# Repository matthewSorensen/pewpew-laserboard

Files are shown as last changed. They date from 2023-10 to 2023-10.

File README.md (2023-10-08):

# PewPew LaserBoard

## What Is It?

LaserBoard is an open source controller for fiber laser marking systems, based around a Teensy 4.1 MCU board. LaserBoard
provides a USB interface compatible with most low-cost fiber laser sources and XY-100-speaking galvanometer scanners, and
supports 4 axes of step/direction motion control. LaserBoard is released under the terms of CERN-OHL-S; see LICENSE.txt,
or [cern_ohl_s_v2.txt](https://ohwr.org/cern_ohl_s_v2.txt) for the full text.

## Q&A

### Why?

At the component level, laser marking hardware is remarkably cheap and high quality, and easy to interface with. Sadly, laser
marker control boards aren't! Generally, they're bundled with a license for low-quality, proprietary software,
greatly inflating the price - a control board with 4 auxiliary axes (eg. JCZ DLC2-M4) cost about as much as a quality
laser source and scanner ($2000!).

Advanced features such as high-precision lens calibration, field stitching, active z-axes control etc. are also very
difficult to implement, as the commercial controllers behave like a black-box and speak an undocumented host/controller
protocol. Some reverse-engineered 3rd party software exists, such as [LightBurn](https://lightburnsoftware.com/) (commercial,
user-friendly high-quality GUI) or [Balor](https://www.bryce.pw/engraver.html) (open-source python interface library),
but controller support is limited.

### Lasers Are Dangerous! Is This Safe?

Lasers can be very dangerous! Unenclosed 10+ watt invisible lasers with peak powers in the low 10s of kW are
absolutely not safe, and a quick scan of YouTokstagram "laser influencer" content will show many poorly educated people
doing very dangerous things with them. Laser safety regulation and enforcement hasn't caught up to the ease with
which anyone can import a turnkey class-4 laser capable of instablindess.

Lasers are also very useful and all of the risks associated with them may be mitigated with proper engineering and
procedural controls. It is essential to fully understand these risks BEFORE purchasing a laser, and if you already
have one, before modifying it or further using it.

If you're in a context with a laser safety officer, talk with them. Laser safety officers are your friends, even
if they seem scary at first.

### What Software Do I Need?

LaserBoard is designed for use with [pewpew-laser](https://github.com/matthewSorensen/pewpew-laser). If that link
appears to be a 404, it's because I'm ambivalent about running an open-source project and haven't figured out the
liability issues related to releasing a complete system. Additionally, there's no GUI or even a standard toolpath
generation script - although there might be some [Rhinoceros](https://www.rhino3d.com/) plugins in the works.

### What Hardware Do I Need?

The following table provides an estimate for a minimal laser marking system with a small Q-switched laser
source, a 50x50 working envelope, a mid-market galvo scanner, and a manually-focused z axis.

|Component |Example Manufacturer and PN|Budgetary Price |
|---|---|---|
|Control Board PCB | LaserBoard-Rev5 |$5-50 |
|Control Board Components | Mouser | $90 |
|30W Laser Source | Raycus - RFL-P30QS | $1000 |
|Galvo Scanner | Sino-Galvo SG7110 | $400 |
|F-theta Lens | HY-SL-1064-50-63 | $70 |
|Beam Path | "Fiber Laser Beam Path" | $70 |
|Stand | "Laser Fiber Lift Table" | $120 |
|350W 24V Power Supply | Meanwell LRS-350-24 | $35 |
|2x 15V 2A Power Supplies | CUI VGS-35C-15 | $28 |

Coincidentally, this comes to around $1850 - around $900 cheaper than a plug-and-play commercial system with
roughly the same grade of component. There does seem to be a large amount of price flexibility on laser sources
from certain AliBaba vendors, to the extent that some JPT MOPA sources may be available for around 50% of list price.
However, importing laser sources can pose significant customs issues. Note that this does not include key safety
equipment, such as an enclosure, properly rated laser safety glasses, or an adequate ventilation system; not does
it include wires, terminal blocks, etc.

## Revision History

### Rev 5a

Revision 5a is a minor revision, primarily fixing screwups in Revision 5. The major changes are as follows:

* Pulldown resistors were added to laser output pins, as turn-on behaviour was undefined.

* Board footprint expanded to keep both DB connector faces in-plane and space
was added between the connectors to accommodate cable's overmolded plastic.

* C15 was switched from an SMD part to a PTH part to simplify soldering.

* The pull-up/pull-down selection jumpers for inputs actually work with the
debouncing network and don't require bodge wires.

* The ethernet status LED is routed to the correct pins on the magjack.

### Rev 5

Revision 5 is, in some ways, a simplification, and breaks pin mapping backwards compatibility. The major
changes are as follows:

* The MCU board is changed from a Teensy 4.0 to a Teensy 4.1, in order to access more GPIO and remove a messy SMD
 header on the bottom of the board.

* Proper power supply input - small fiber lasers generally run on 24VDC supplies, and galvo scanners required -15/15V
 supplies, so there's always a readily available DC rail to generate a 5V rail for the teensy. The input protection
 circuit and switcher is essentially the same as published [here](https://blog.thea.codes/starfish-a-control-board-with-the-rp2040/),
 although it omits reverse polarity protection and uses a small polyfuse due to much lower current demands. The board
 may also be powered off a USB connection by shifting the location of a jumper.

* The Q-switch protection circuitry is removed, as the current firmware seems to be robust enough to trust with not
 generating Q-switch clock glitches, and the broader frequency range required for MOPA sources renders it useless.

* Previously, the standard 8-bit parallel laser power interface used a shift register to reduce the GPIO requirement - now,
  8 GPIO pins directly control the power. Supporting MOPA serial data stream with the shift register would have
  required bit-banging a serial stream to bit bang a serial stream - although this was technically feasible, the code
  complexity would have been annoying, and the switch to a parallel interface only required four extra pins.

* Four limit pins are properly debounced with a low-pass filter and Schmitt-trigger and have (jumper) configurable
  pull-up/down resistors and indicator LEDs.

* The teensy 4.1 ethernet phy is broken out to an on-board magjack.

### Rev 4

Rev 4 fixed a bodge wire needed for rev 3 and slightly modified the laser pinout to
support JPT long-pulse sources, although that is as of yet untested.

### Rev 3

Rev 2 incorporated the following changes:

* Support for a two-axis galvanometer scanner communicating over XY-100, requiring
  adding a DB-15 interface and four differential line drivers.
* Motor interfaces were moved to 4 polarized 4 pin molex 0,1" headers.

Rev 3 is still in active use.

### Rev 1 and 2

Revision one was ordered 2021/5/4, and had the following features:

* One DB-25 interface for a q-switched fiber laser, with a one-shot timer
  used to protect the laser from abnormal q-switch pulse trains, a shift
  register for the power control interface, and a hardware interlock to
  require a good q-switch clock signal, a good e-stop signal, and software
  enabling of the laser.
* Four step/direction interfaces, level-shifted to 5V and broken out on a
  single 0.1" header.
* A schmitt-triggered and debounced e-stop input.
* 9 GPIO broken out on a 0.1" header, with no level-shifting or signal conditioning.

Revision one was used with a stepper-driven micrometer stage to get a proof-of-concept
working for some surface-patterning applications, and was quickly replaced with rev 2 -
seemingly a mostly cosmetic modification .

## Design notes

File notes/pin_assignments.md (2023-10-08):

# LaserBoard Pin Assignments

## Laser Source IO

Most of the laserboar-r5's GPIO is spent on a semi-universal interface for common fiber laser sources. None of these
pins have strict hardware interface, although SYNC must be a PWM-capable pin. 

|IO Name/Function|Teensy 4.1 Pin Number|Register/Bit|
|---|---|---|
|INTERLOCK |6 |GPIO7/10 |
|ENABLE |8 |GPIO7/16 |
|GUIDE_LASER |9 |GPIO7/11 |
|ALARM_0/LATCH |10 |GPIO7/0 |
|SYNC |11 |GPIO7/2 |
|MODULATE |12 |GPIO7/1 |
|ALARM_2 |26 |GPIO6/30 |
|ALARM_1 |27 |GPIO6/31 |
|PWR_0 |33 |GPIO9/7 |
|PWR_1/SER_DATA  |34 |GPIO8/15 |
|PWR_2/SER_CLOCK |35 |GPIO8/14 |
|PWR_3 |36 |GPIO8/13 |
|PWR_4 |28 |GPIO8/18 |
|PWR_5 |29 |GPIO9/31 |
|PWR_6 |30 |GPIO8/23 |
|PWR_7 |31 |GPIO8/22 |

INTERLOCK is an input pin for an enclosure interlock switch (active closed, labeled "Interlock" on PCB), which is
debounced and level-shifted to 3.3v. This signal is also level-shifted to 5V and routed to the laser's interlock
pin (thought jumper JP11), and has an associated indicator LED (labeled "Interlock OK!"). ENABLE is an
(active-high) output pin for the controller to arm the laser - the actual enable signal is derived by passing this
and the INTERLOCK signal through an AND-gate.

GUIDE_LASER is an active-high output for the laser source's aiming laser, if one exists. Note that this has no
interlock, as it is intended for use with an open enclosure. On most MOPA sources, this also puts the source
into receive mode for the serial data stream on PWR_1/SER_DATA & PWR_2/SER_CLOCK - thus, firmware must not change
any power levels while GUIDE_LASER is high.

SYNC is the laser pulse clock - unlike previous revisions, there is no hardware timer supervising this, and so it
must not be changed while the laser is actively firing, or giant Q-switch pulses may destroy optics. Pulse
repetition rate is highly source dependent, but the teensy 4.x can generate PWM at up to 10s of MHz, and the
74AHC245PW is similarly capable.

Once a laser source is armed (INTERLOCK is high, ENABLE is high, SYNC is running, and a suitable lockout period
has passed), MODULATE is an active-high pin that controls laser emission.

On some laser sources, ALARM_0/LATCH is a controller input that sources may use to signal undervoltage conditions.
It is also multiplexed as a latch signal for sources that require one - JP13 controls this, and defaults to closed/alarm
mode.

PWR_0 through PWR_7 form a 8-bit parallel interface for laser power control, with a least-significant bit of PWR_0. MOPA
laser sources also support a serial data input stream for configuring pulse length - in that case, serial data may be
written at 8kHz over PWR_1/SER_DATA and PWR_1/SER_CLOCK when the GUIDE_LASER line is high. In all cases, the power bits
may not change when the laser is emitting.

## Galvo XY-100 IO

The galvo IO needs to be on these exact pins, as it uses the Teensy's I2S hardware to generate all signals. 
The interface to the galvos is made through two UA9638CD differential line drivers, each taking two single-ended
signals from the processor and turning them into differential signals for the galvos. These are all verified to be
compatible between teensy 4, 4.1, and Teensy Micromod.

|IO Name/Function|Teensy 4.1 Pin Number|Register/Bit|
|---|---|---|
|GALVO_CLOCK |21 |**GPIO6/27** |
|GALVO_SYNC |20 |**GPIO6/26** |
|GALVO_D1 |7 |**GPIO7/17** |
|GALVO_D2 |32 |**GPIO7/12** |

## Motion IO

The step and direction GPIO must all lie on one port - in this case, GPIO6. This is the main limit to the number of
stepper axes, and could be expanded by refactoring the code to only require that the step pins lie on one port, and
the direction pins on another. Similarly, the limit switch pins must all lie on one port - this is less critical, and
would be easy to refactor away from. 

Electrically, step/dir pins are level shifted to 5V with a 74AHC245PW-Q100J. Limit switches are debounced with a slightly
elaborate arrangement of an RC low-pass filter, jumper-configurable pull-ups/pull-downs with diodes for symmetric recovery,
and another 74AHC245PW Schmitt-trigger.

|IO Name/Function|Teensy 4.1 Pin Number|Register/Bit|
|---|---|---|
|Axis 0 Step |23 |**GPIO6/25** |
|Axis 0 Direction|22 |**GPIO6/24** |
|Axis 0 Home |2 |**GPIO9/4** |
|Axis 1 Step |19 |**GPIO6/16** |
|Axis 1 Direction|18 |**GPIO6/17** |
|Axis 1 Home |3 |**GPIO9/5** |
|Axis 2 Step |17 |**GPIO6/22** |
|Axis 2 Direction|16 |**GPIO6/23** |
|Axis 2 Home |4 |**GPIO9/6** |
|Axis 3 Step |15 |**GPIO6/19** |
|Axis 3 Direction|14 |**GPIO6/18** |
|Axis 3 Home |5 |**GPIO9/8** |

# Laser DB-25 Interface

| DB-25 Pin | Raycus RFL-P30QS | JPT YDFLP-E-20 | RFL-P20MB | JPT  YDFLP-M6+ | Current Pinout |
| --- | --- | --- | --- | --- | --- |
| 1 | Power LSB - D0 | Power LSB - D0 | Power LSB - D0 | Power LSB - D0 | PWR_0 |
| 2 | D1 | D1 | D1 / Serial Input | D1 / Serial Input | PWR_1/SER_DATA | 
| 3 | D2 | D2 | D2 / Serial Clock | D2 / Serial Clock | PWR_2/SER_CLOCK |
| 4 | D3 | D3 | D3 | D3 | PWR_3 |
| 5 | D4 | D4 | D4 | D4 | PWR_4 |
| 6 | D5 | D5 | D5 | D5 | PWR_5 |
| 7 | D6 | D6 | D6 | D6 | PWR_6 |
| 8 | Power MSB - D7 | Power MSB - D7 | Power MSB - D7 | Power MSB - D7 | PWR_7 |
| 9 | Obligate Raycus only | Power Latch | Obligate Raycus only | NC | Multiplexed to ALARM_O/LATCH |
| 10 | GND | GND | GND | GND | GND |
| 11 | Supply voltage alarm | GND | Abnormal state alarm | GND | Multiplexed to ALARM_O/LATCH |
| 12 | alarm - always high | GND | alarm - always high | GND | NC |
| 13 | GND | GND | Obligate Raycus only | GND | NC |
| 14 | GND | GND | GND | GND | GND |
| 15 | GND | GND | Obligate Raycus only | GND | NC |
| 16 | System Alarm | System Alarm | System Alarm | System Alarm | ALARM_1 |
| 17 | 5V Supply | NC | 5V Supply | NC | Jumper to 5V supply |
| 18 | Emission Enable | Master Oscilator enable | Emission Enable | Master Oscilator enable | SAFE_ENABLE |
| 19 | Emission Modulate | Emission Modulation | Emission Modulate | Emission Modulation | MODULATE |
| 20 | Sync | Frequency Modulation | Sync | Frequency Modulation | SYNC |
| 21 | Alarm | Temperature Alarm | Alarm | Temperature Alarm | ALARM_2 |
| 22 | Guide Laser | Guide Laser | Guide Laser / Serial Enable | Guide Laser / Serial Enable | GUIDE_LASER |
| 23 | Obligate Raycus only | Emergency Stop | Obligate Raycus only | NC | Jumper to INTERLOCK |
| 24 | GND | NC | Obligate Raycus only | NC | NC |
| 25 | GND | NC | Obligate Raycus only | NC | NC |

# Jumper Table

|Jumper Designators|Function|Default|Raycus State|JPT State| 
|---|---|---|---|---|
|JP14,15| Limit input 0 pull up|closed|n.a.|n.a|
|JP1,2| Limit input 0 pull down|open|n.a.|n.a|
|JP3,17| Limit input 1 pull up|closed|n.a.|n.a|
|JP4,16| Limit input 1 pull down|open|n.a.|n.a|
|JP5,19| Limit input 2 pull up|closed|n.a.|n.a|
|JP6,18| Limit input 2 pull down|open|n.a.|n.a|
|JP7,21| Limit input 3 pull up|closed|n.a.|n.a|
|JP8,20| Limit input 3 pull down|open|n.a.|n.a|
|JP9| Laser 5V supply| closed | closed | open|
|JP10| Power Latch | open | open | closed |
|JP11| Interlock/E-stop | closed | closed | closed |
|JP12| USB Power | n.a. | n.a. | n.a. |
|JP13| Alarm 0 |closed | closed | open |

Only one of each pair of JP1/JP2, etc should be closed for proper limit operation. For programming and
operation on USB power, JP12 must have pins 1 and 2 connected. For operation on external power, JP12 must
have pins 2 and 3 connected.

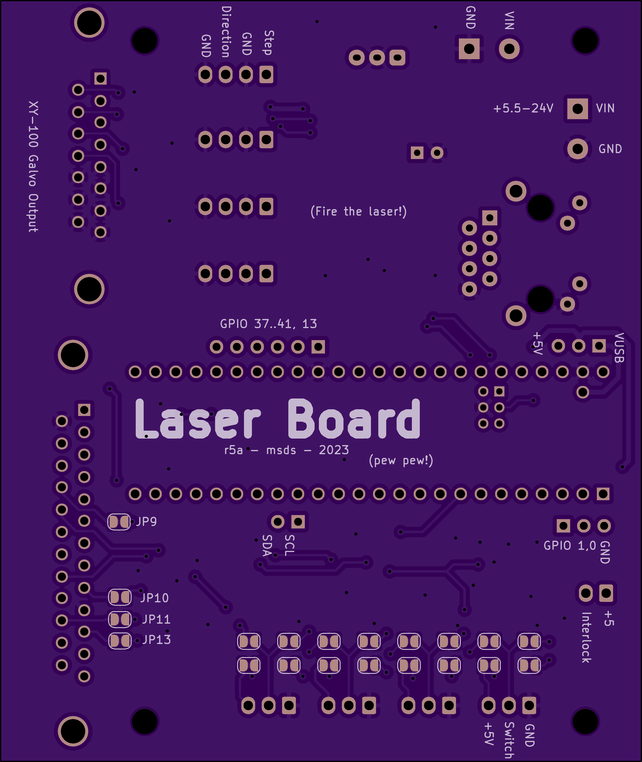
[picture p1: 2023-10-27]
exports/LaserBoardR5a-Back.png

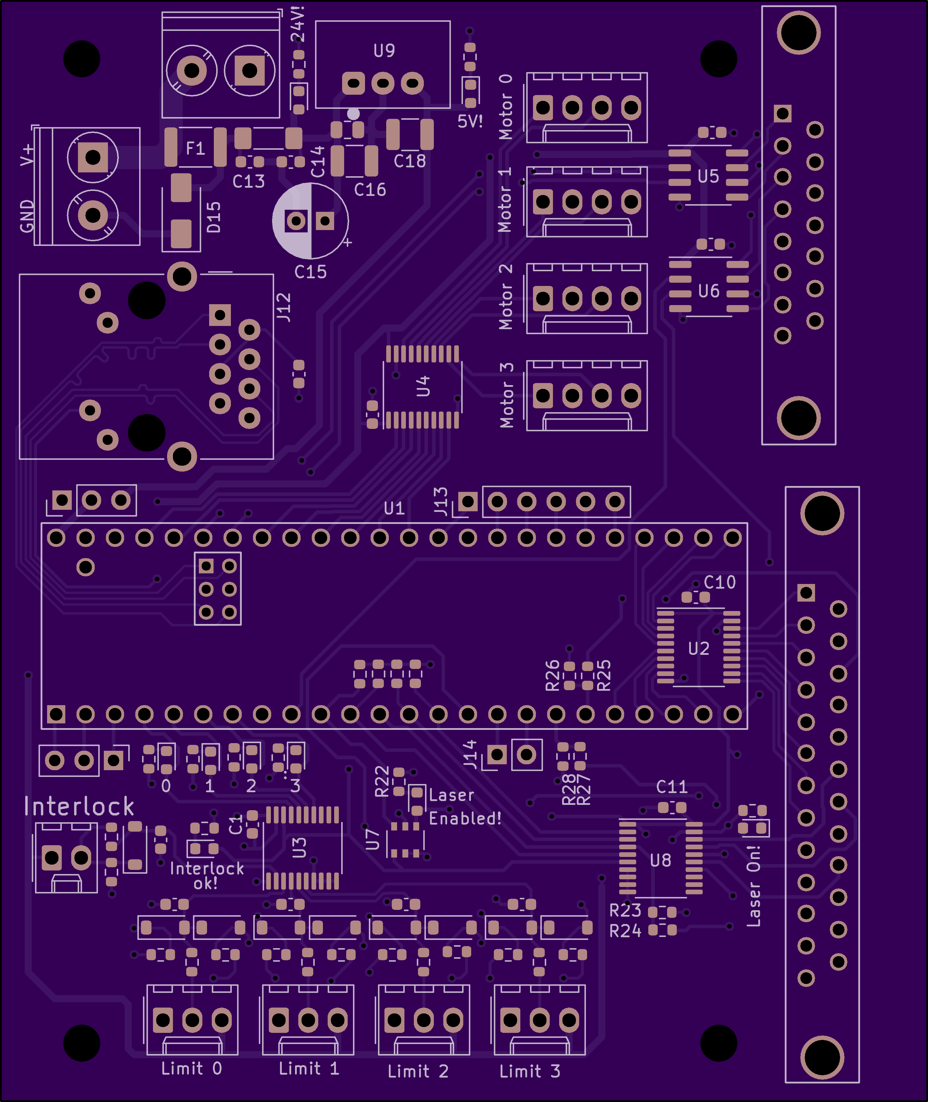
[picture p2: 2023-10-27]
exports/LaserBoardR5a-Front.png

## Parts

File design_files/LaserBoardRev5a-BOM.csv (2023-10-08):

Reference | Value | Mouser Part Number | Manufacturer Part Number | Qty | Notes
C1, C7-C11 | 0.1uF, 25V | 187-CL05A104KA5NNNC | CL05A104KA5NNNC | 6 | Generic decoupling cap
C2-C6 | 1uF | 810-CGA3E1X7R1C105AC | CGA3E1X7R1C105AC | 5
C12-C14 | 0.1uF, 50V | 80-C603C104K5RAC3121 | C603C104K5RAC3121 | 3
C15 | 100uF, 35V | 710-860040573004 | 860040573004 | 1
C16, C18 | 10uF 35V | 187-CL32A106KAULNNE | CL32A106KAULNNE | 2
C17 | 4.7uF 35V | 187-CL21A475KLCLQNC | CL21A475KLCLQNC | 1
D1-D8, D10 | 1N4148W-7-F | 621-1N4148W-F | 1N4148W-F | 9
D9 | RED LED | 710-150060RS75000 | 150060RS75000 | 1
D11-D14, D16-D18 | GREEN LED | 710-150060GS75000 | 150060GS75000 | 7
D15 | SMAJ28CA | 576-SMAJ28CA | SMAJ28CA | 1
D19 | BLUE LED | 710-150060BS75000 | 150060BS75000 | 1
F1 | 300mA PPTC | 650-MINISMDC030F-2 | MINISMDC030F-2 | 1
FB1 | 60R @ 100MHz, 6A | 81-BLM41P600S | BLM41PG600SN1L | 1
J1-J4 | Type KK 1x03 Socket | 710-61900311121 | 61900311121 | 4
J5 | Type KK 1x02 Socket | 710-61900211121 | 61900211121 | 1
J6-J9 | Type KK 1x04 Socket | 710-61900411121 | 61900411121 | 4
J10 | DA15_Receptacle | 710-618015231321 | 618015231321 | 1
J11 | DB25_Receptacle | 710-618025231121 | 618025231121 | 1
J12 | RJ45_Amphenol_RJMG1BD3B8K1ANR | 710-618015231321 | 618015231321 | 1
J17, J18 | Screw_Terminal_01x02 | 490-TB002-500-02BE | TB002-500-02BE | 2
R1-R12, R14, R15, R24, R25, R27, R30-R33 | R10K | 603-RC0603JR-0710KL | RC0603JR-0710KL | 21
R13, R16-R23, R26, R28, R29 | R20K | 603-RC0603JR-0720KL | RC0603JR-0720KL | 12
U1 | Teensy4.1 | 474-DEV-16771 | TEENSY41 | 1 | Don't purchase from Mouser - export control paperwork is slow
U2-U4, U8 | 74HC245 | 771-74AHC245PW-Q100J | 74AHC245PW-Q100J | 4
U5, U6 | UA9638CDR | 595-UA9638CDR | UA9638CDR | 2
U7 | 74LVC1G3208 | 595-SN74LC1G3208DBVR | SN74LC1G3208DBVR | 1
U9 | VX7805-500 | 490-VX7805-500 | VX7805-500 | 1
Teensy Ethernet Header | 2x3 2mm Pitch Header | 571-2MM-HBD03VT02HTB | 2MM-HBD03VT02HTB | 1 | Alternately, purchase 1x ETHERNET_KIT from PJRC, and skip J12
JP12, J13,J14,J15, Teensy Headers | 1x24 0.1" Breakaway Headers | 538-22-28-4244 | 22-28-4244 | 3
Jumper for power | 0.1" Jumper | 710-60900213421 | 60900213421 | 1
External Connectors | External Connectors
Reference | Value | Mouser Part Number | Manufacturer Part Number | Qty | Notes
J1-J4 | Type KK 1x03 Terminal Housing | 710-61900311621 | 61900311621 | 4
J5 | Type KK 1x02 Terminal Housing | 710-61900211621 | 61900211621 | 1
J6-J9 | Type KK 1x04 Terminal Housing | 710-61900411621 | 61900411621 | 4
 | Female Crimp Contact | 710-61900113722DEC | 61900113722DEC | 33

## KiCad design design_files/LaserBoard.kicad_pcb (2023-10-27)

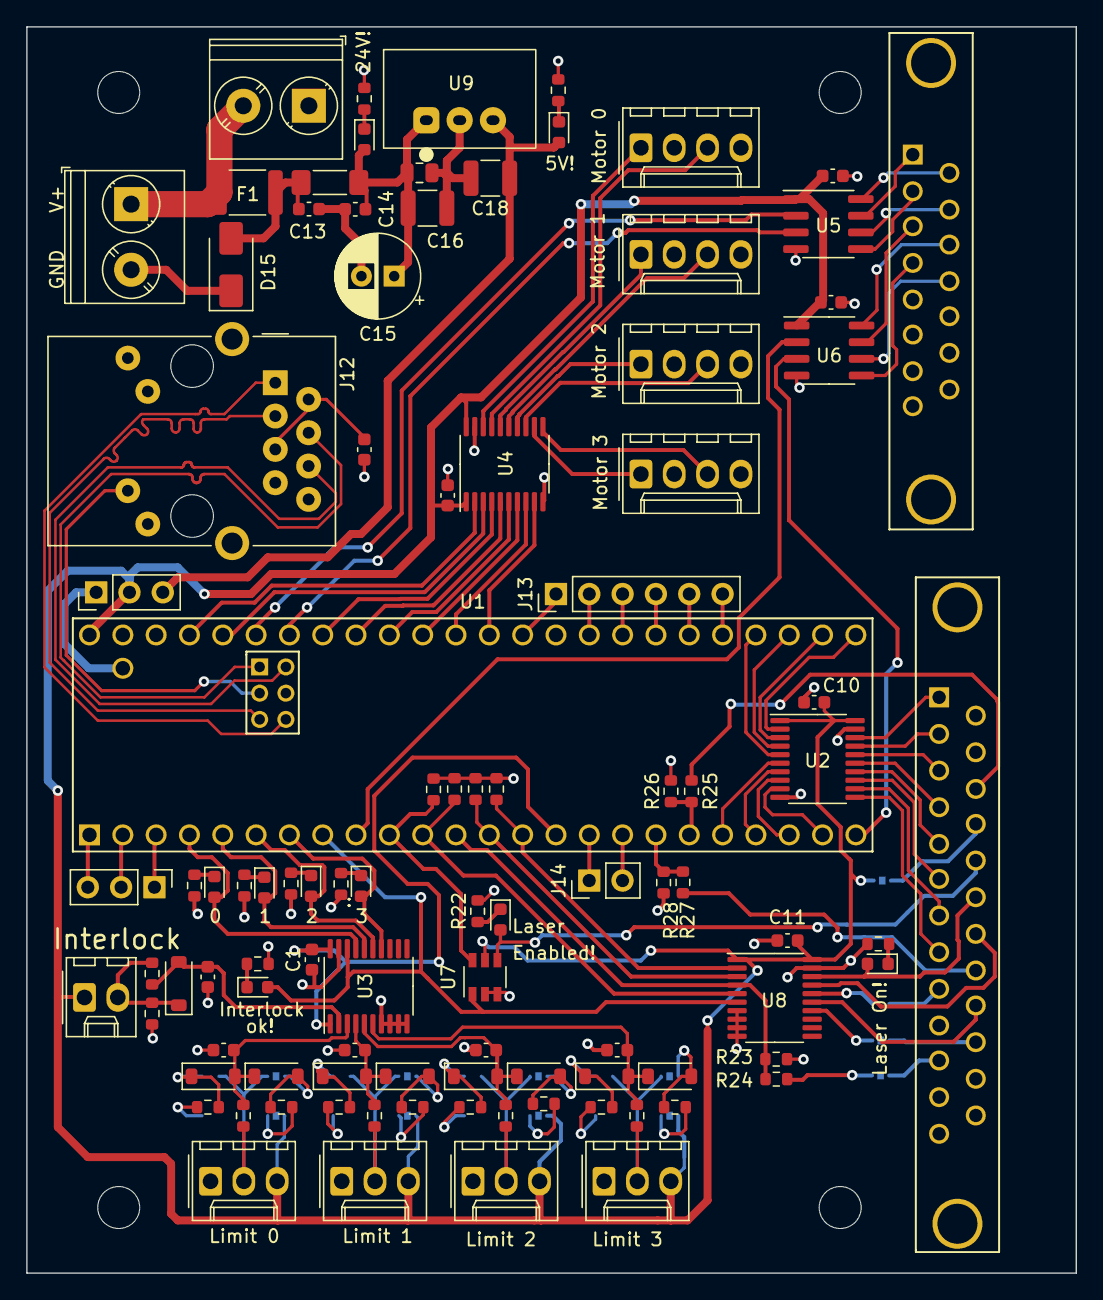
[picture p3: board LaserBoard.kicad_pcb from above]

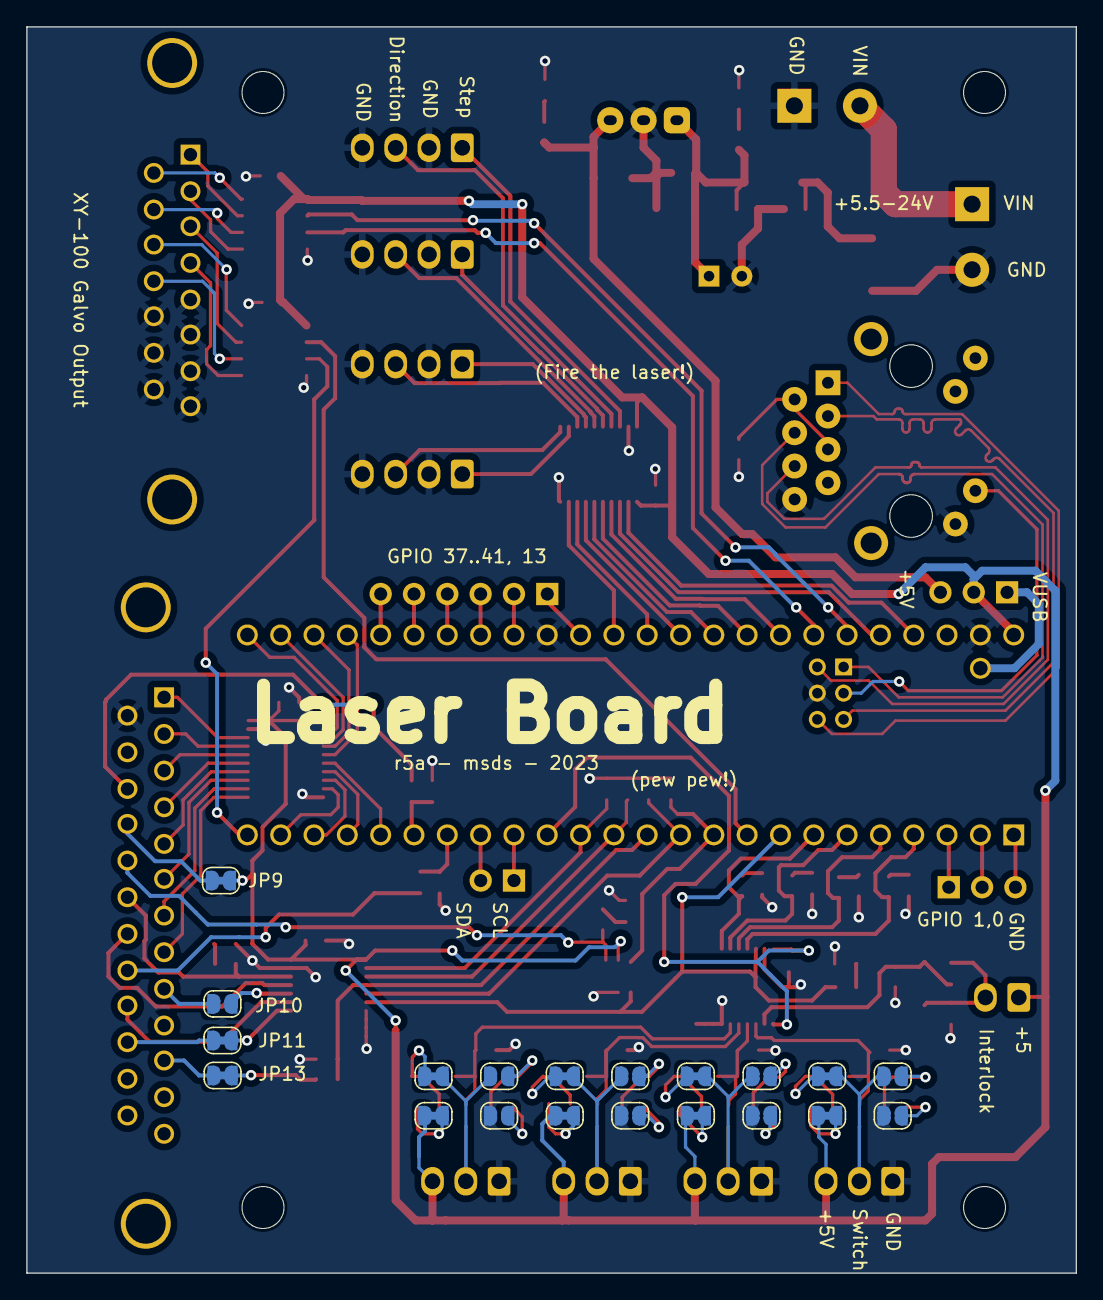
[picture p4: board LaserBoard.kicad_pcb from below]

Board: 2 copper layers, 80.0 x 95.0 mm, 123 parts (20 on the bottom side), 129 nets.

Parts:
C1, C7, C8, C9, C10, C11: 0.1uF, 25V; C_0603_1608Metric
C2, C3, C4, C5, C6: 1uF; C_0603_1608Metric
C12, C13, C14: 0.1uF, 50V; C_0603_1608Metric
C15: 100uF, 35V; CP_Radial_D6.3mm_P2.50mm
C16, C18: 10uF 35V; C_1210_3225Metric
C17: 4.7uF 35V; C_0805_2012Metric
D1, D2, D3, D4, D5, D6, D7, D8, D10: 1N4148W-7-F; D_SOD-123
D9: RED LED; LED_0603_1608Metric
D11, D12, D13, D14, D16, D17, D18: GREEN LED; LED_0603_1608Metric
D15: SMAJ28CA; D_SMA
D19: BLUE LED; LED_0603_1608Metric
F1: 300mA PPTC; R_1812_4532Metric
FB1: 60R @ 100MHz, 6A; L_1806_4516Metric_Pad1.45x1.90mm_HandSolder
H1, H2, H3, H4: MountingHole; MountingHole_3.2mm_M3_DIN965
J1, J2, J3, J4: Type KK 1x03 Socket; Molex_KK-254_AE-6410-03A_1x03_P2.54mm_Vertical
J5: Type KK 1x02 Socket; Molex_KK-254_AE-6410-02A_1x02_P2.54mm_Vertical
J6, J7, J8, J9: Type KK 1x04 Socket; Molex_KK-254_AE-6410-04A_1x04_P2.54mm_Vertical
J10: DA15_Receptacle; DB15FD
J11: DB25_Receptacle; DB25FD
J12: RJ45_Amphenol_RJMG1BD3B8K1ANR
J13: Conn_01x06; PinHeader_1x06_P2.54mm_Vertical
J14: Conn_01x02_Pin; PinHeader_1x02_P2.54mm_Vertical
J15: Conn_01x03; PinHeader_1x03_P2.54mm_Vertical
J17, J18: Screw_Terminal_01x02; TerminalBlock_Phoenix_PT-1,5-2-5.0-H_1x02_P5.00mm_Horizontal
JP1, JP2, JP4, JP6, JP8, JP10, JP16, JP18, JP20: Jumper 2 Position, Open; SolderJumper-2_P1.3mm_Open_RoundedPad1.0x1.5mm
JP3, JP5, JP7, JP14, JP15, JP17, JP19, JP21: Jumper_2_Bridged; SolderJumper-2_P1.3mm_Bridged_RoundedPad1.0x1.5mm
JP9, JP11, JP13: Jumper 2 Position, Closed; SolderJumper-2_P1.3mm_Bridged_RoundedPad1.0x1.5mm
JP12: Jumper 3 Position, Open; PinHeader_1x03_P2.54mm_Vertical
R1, R2, R3, R4, R5, R6, R7, R8, R9, R10, R11, R12, R14, R15, R24, R25, R27, R30, R31, R32, R33: R10K; R_0603_1608Metric
R13, R16, R17, R18, R19, R20, R21, R22, R23, R26, R28, R29: R20K; R_0603_1608Metric
U1: Teensy4.1; Teensy41
U2, U3, U4, U8: 74HC245; TSSOP-20_4.4x6.5mm_P0.65mm
U5, U6: UA9638CDR; SOIC-8_3.9x4.9mm_P1.27mm
U7: 74LVC1G3208; TSOP-6_1.65x3.05mm_P0.95mm
U9: VX7805-500; Converter_DCDC_CUI_VX78-500_THT

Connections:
5V_SUPPLY: C18.1, D16.2 (A), JP12.3 (B), U9.3 (Vout)
+3.3V: C1.2, U1.15 (3V3), U3.1 (A->B), U3.20 (VCC)
+5V: C7.2, C8.1, C9.1, C10.1, C11.2, J1.3, J2.3, J3.3, J4.3, J5.1, JP3.1 (A), JP5.1 (A), JP7.1 (A), JP9.1 (A), JP12.2 (C), JP14.1 (A), U1.48 (VIN), U2.1 (A->B), U2.20 (VCC), U4.1 (A->B), U4.20 (VCC), U5.1 (VCC), U6.1 (VCC), U7.5 (VCC), U8.1 (A->B), U8.20 (VCC)
+24V: C14.1, C15.1, C16.1, C17.2, D17.2 (A), FB1.1, U9.1 (Vin)
/R+: J12.R4 (RD+), U1.60 (R+)
/R-: J12.R6 (RD-), U1.65 (R-)
/T+: J12.R1 (TD+), U1.63 (T+)
/T-: J12.R3 (TD-), U1.62 (T-)
ALARM_0_5V: J11.11, JP13.2 (B)
ALARM_0/POWER_LATCH: R23.1, R24.2, U1.12 (10_CS_MQSR), U8.4 (A2)
ALARM_1: R25.2, R26.1, U1.19 (27_A13_SCK1)
ALARM_1_5V: J11.16, R25.1
ALARM_2: R27.2, R28.1, U1.18 (26_A12_MOSI1)
ALARM_2_5V: J11.21, R27.1
DIR0: U1.44 (22_A8_CTX1), U4.3 (A1)
DIR1: U1.40 (18_A4_SDA), U4.5 (A3)
DIR2: U1.38 (16_A2_RX4_SCL1), U4.7 (A5)
DIR3: U1.36 (14_A0_TX3_SPDIF_OUT), U4.9 (A7)
ENABLE: R30.1, U1.10 (8_TX2_IN1), U7.6
GALVO_CLOCK: U1.43 (21_A7_RX5_BCLK1), U5.2 (IN)
GALVO_D1: U1.9 (7_RX2_OUT1A), U6.2 (IN)
GALVO_D2: U1.24 (32_OUT1B), U6.3 (IN)
GALVO_SYNC: U1.42 (20_A6_TX5_LRCLK1), U5.3 (IN)
GND: C1.1, C2.2, C3.2, C4.2, C5.2, C6.2, C7.1, C8.2, C9.2, C10.2, C11.1, C12.1, C13.2, C14.2, C15.2, C16.2, C17.1, C18.2, D15.1 (A1), J1.1, J2.1, J3.1, J4.1, J6.2, J6.4, J7.2, J7.4, J8.2, J8.4, J9.2, J9.4, J10.5, J10.6, J10.7, J10.8, J10.13, J10.14, J10.15, J11.10, J11.14, J12.L1 (LEDY_A), J12.R8 (GND), J17.1, J18.2, JP2.2 (B), JP4.2 (B), JP6.2 (B), JP8.2 (B), R13.2, R14.1, R16.2, R17.2, R18.2, R19.2, R20.1, R21.1, R22.2, R23.2, R26.2, R28.2, R29.2, R30.2, R31.1, R32.1, R33.1, U1.34 (GND), U1.47 (GND), U1.64 (GND), U2.10 (GND), U2.19 (CE), U3.7 (A5), U3.8 (A6), U3.9 (A7), U3.10 (GND), U3.19 (CE), U4.10 (GND), U4.19 (CE), U5.4 (GND), U6.4 (GND), U7.2 (GND), U7.3, U8.7 (A5), U8.8 (A6), U8.9 (A7), U8.10 (GND), U8.19 (CE), U9.2 (GND)
GUIDE_LASER: R31.2, U1.11 (9_OUT1C), U8.5 (A3)
INTERLOCK: D9.2 (A), U1.8 (6_OUT1D), U3.18 (B0), U7.1, U8.6 (A4)
LIMIT0: D14.2 (A), U1.4 (2_OUT2), U3.17 (B1)
LIMIT1: D13.2 (A), U1.5 (3_LRCLK2), U3.16 (B2)
LIMIT2: D12.2 (A), U1.6 (4_BCLK2), U3.15 (B3)
LIMIT3: D11.2 (A), U1.7 (5_IN2), U3.14 (B4)
MODULATE: R33.2, U1.14 (12_MISO_MQSL), U8.2 (A0)
unnamed: D1.2 (A), JP15.1 (A), R2.2
unnamed: C2.1, D1.1 (K), D2.2 (A), R1.2, U3.3 (A1)
unnamed: D2.1 (K), JP1.1 (A), R3.2
unnamed: D3.2 (A), JP17.1 (A), R4.2
unnamed: C3.1, D3.1 (K), D4.2 (A), R6.2, U3.4 (A2)
unnamed: D4.1 (K), JP16.1 (A), R5.2
unnamed: D5.2 (A), JP19.1 (A), R7.2
unnamed: C4.1, D5.1 (K), D6.2 (A), R11.2, U3.5 (A3)
unnamed: D6.1 (K), JP18.1 (A), R8.2
unnamed: D7.2 (A), JP21.1 (A), R9.2
unnamed: C5.1, D7.1 (K), D8.2 (A), R12.2, U3.6 (A4)
unnamed: D8.1 (K), JP20.1 (A), R10.2
unnamed: D9.1 (K), R13.1
unnamed: C6.1, D10.2 (A), R15.2, U3.2 (A0)
unnamed: D10.1 (K), J5.2, R14.2, R15.1
unnamed: D11.1 (K), R16.1
unnamed: D12.1 (K), R17.1
unnamed: D13.1 (K), R18.1
unnamed: D14.1 (K), R19.1
unnamed: D16.1 (K), R20.2
unnamed: D17.1 (K), R21.2
unnamed: D18.1 (K), R22.1
unnamed: D19.2 (A), J11.19, U8.18 (B0)
unnamed: D19.1 (K), R29.1
unnamed: J1.2, JP1.2 (B), JP15.2 (B), R1.1
unnamed: J2.2, JP16.2 (B), JP17.2 (B), R6.1
unnamed: J3.2, JP18.2 (B), JP19.2 (B), R11.1
unnamed: J4.2, JP20.2 (B), JP21.2 (B), R12.1
unnamed: J6.1, U4.18 (B0)
unnamed: J6.3, U4.17 (B1)
unnamed: J7.1, U4.16 (B2)
unnamed: J7.3, U4.15 (B3)
unnamed: J8.1, U4.14 (B4)
unnamed: J8.3, U4.13 (B5)
unnamed: J9.1, U4.12 (B6)
unnamed: J9.3, U4.11 (B7)
unnamed: J10.9, U5.8 (OUTB)
unnamed: J10.10, U5.6 (OUTB)
unnamed: J10.12, U6.6 (OUTB)
unnamed: J10.11 (P111), U6.8 (OUTB)
unnamed: J11.17, JP9.2 (B)
unnamed: J11.20, U8.17 (B1)
unnamed: J11.22, U8.15 (B3)
unnamed: J11.23, JP11.2 (B)
unnamed: J12.L2 (LEDY_K), U1.61 (LED)
unnamed: C12.2, J12.R2 (TCT), J12.R5 (RCT)
unnamed: J13.1, U1.35 (13_SCK_LED)
unnamed: J13.2, U1.33 (41_A17)
unnamed: J13.3, U1.32 (40_A16)
unnamed: J13.4, U1.31 (39_MISO1_OUT1A)
unnamed: J13.5, U1.30 (38_CS1_IN1)
unnamed: J13.6, U1.29 (37_CS)
unnamed: J14.1, U1.16 (24_A10_TX6_SCL2)
unnamed: J14.2, U1.17 (25_A11_RX6_SDA2)
unnamed: J15.1, U1.3 (1_TX1_CTX2_MISO1)
unnamed: J15.2, U1.2 (0_RX1_CRX2_CS1)
unnamed: J15.3, U1.1 (GND)
unnamed: JP2.1 (A), R3.1
unnamed: JP3.2 (B), R4.1
unnamed: JP4.1 (A), R5.1
unnamed: JP5.2 (B), R7.1
unnamed: JP6.1 (A), R8.1
unnamed: JP7.2 (B), R9.1
unnamed: JP8.1 (A), R10.1
unnamed: JP10.1 (A), U8.16 (B2)
unnamed: J11.9, JP10.2 (B)
unnamed: JP11.1 (A), U8.14 (B4)
unnamed: JP12.1 (A), U1.49 (VUSB)
unnamed: JP13.1 (A), R24.1
unnamed: JP14.2 (B), R2.1
unnamed: J11.1, U2.18 (B0)
unnamed: J11.2, U2.17 (B1)
unnamed: J11.3, U2.16 (B2)
unnamed: J11.4, U2.15 (B3)
unnamed: J11.5, U2.14 (B4)
unnamed: J11.6, U2.13 (B5)
unnamed: J11.7, U2.12 (B6)
unnamed: J11.8, U2.11 (B7)
unnamed: J10.1, U5.7 (OUTA)
unnamed: J10.2, U5.5 (OUTA)
unnamed: J10.3, U6.7 (OUTA)
unnamed: J10.4, U6.5 (OUTA)
PWR_0: U1.25 (33_MCLK2), U2.2 (A0)
PWR_1/SER_DATA: U1.26 (34_RX8), U2.3 (A1)
PWR_2/SER_CLOCK: U1.27 (35_TX8), U2.4 (A2)
PWR_3: U1.28 (36_CS), U2.5 (A3)
PWR_4: U1.20 (28_RX7), U2.6 (A4)
PWR_5: U1.21 (29_TX7), U2.7 (A5)
PWR_6: U1.22 (30_CRX3), U2.8 (A6)
PWR_7: U1.23 (31_CTX3), U2.9 (A7)
RAW_24: C13.1, D15.2 (A2), F1.1, FB1.2
SAFE_ENABLE: D18.2 (A), J11.18, U7.4
STEP0: U1.45 (23_A9_CRX1_MCLK1), U4.2 (A0)
STEP1: U1.41 (19_A5_SCL), U4.4 (A2)
STEP2: U1.39 (17_A3_TX4_SDA1), U4.6 (A4)
STEP3: U1.37 (15_A1_RX3_SPDIF_IN), U4.8 (A6)
SYNC: R32.2, U1.13 (11_MOSI_CTX1), U8.3 (A1)
V_INPUT: F1.2, J17.2, J18.1

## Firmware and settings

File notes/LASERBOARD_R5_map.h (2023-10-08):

/*
  LASERBOARD_R5_map.h - driver code for IMXRT1062 processor (on Teensy 4.0 board)

  Part of grblHAL

  Board by Matthew Sorensen: https://github.com/matthewSorensen/pewpew-laserboard

  Note that this is a board map for using Laserboard-R5 as a generic 5x axis cnc controller,
  not for its intended purpose - driving fiber laser sources and galvo scanners, along
  with 4 axis motion. Some of the capabilities are limited - aux gpio isn't protected,
  the 4th axis limit switch doesn't have a proper debounce circuit, etc.

  Copyright (c) 2020-2023 Terje Io

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
  You should have received a copy of the GNU General Public License
  along with Grbl.  If not, see <http://www.gnu.org/licenses/>.
*/

#define BOARD_NAME "Laserboard-R5"
#define BOARD_URL "https://github.com/matthewSorensen/pewpew-laserboard"

#if N_ABC_MOTORS > 2
#error "Axis configuration is not supported!"
#endif

#if QEI_ENABLE
#error "No pins available for encoder input!"
#endif

#if SPINDLE_SYNC_ENABLE
#error "Spindle sync is not supported for Laserboard-R5!"
#endif

#define X_STEP_PIN          (23u)
#define X_DIRECTION_PIN     (22u)
#define X_LIMIT_PIN         (2u)

#define Y_STEP_PIN          (19u)
#define Y_DIRECTION_PIN     (18u)
#define Y_LIMIT_PIN         (3u)

#define Z_STEP_PIN          (17u)
#define Z_DIRECTION_PIN     (16u)
#define Z_LIMIT_PIN         (4u)

// Define ganged axis or A axis step pulse and step direction output pins.
#if N_ABC_MOTORS > 0
#define M3_AVAILABLE
#define M3_STEP_PIN         (15u)
#define M3_DIRECTION_PIN    (14u)
#define M3_LIMIT_PIN        (10u)
#endif

// Define ganged axis or B axis step pulse and step direction output pins.
#if N_ABC_MOTORS == 2
#define M4_AVAILABLE
#define M4_STEP_PIN         (33u)
#define M4_DIRECTION_PIN    (34u)
#define M4_LIMIT_PIN        (27u)
#define M4_ENABLE_PIN       (35u)
#endif

#if MPG_MODE == 1 && !defined(M4_LIMIT_PIN)
#define MPG_MODE_PIN        (39u)
#endif

// Define stepper driver enable/disable output pin(s).
#define STEPPERS_ENABLE_PIN (36u)

// Define spindle enable and spindle direction output pins.
#if DRIVER_SPINDLE_ENABLE
#define SPINDLE_ENABLE_PIN      (8u)
#define SPINDLE_DIRECTION_PIN   (11u)
#define SPINDLE_PWM_PIN         (12u) // NOTE: only pin 12 or pin 13 can be assigned!
#endif

// Define flood and mist coolant enable output pins.
#define COOLANT_FLOOD_PIN   (28u)
#define COOLANT_MIST_PIN    (29u)

// Define user-control CONTROLs (cycle start, reset, feed hold, door) input pins.
#define RESET_PIN           (26u)
#define FEED_HOLD_PIN       (37u)
#define CYCLE_START_PIN     (38u)
#if SAFETY_DOOR_ENABLE
#define SAFETY_DOOR_PIN     (6u)
#endif

// Define probe switch input pin.
#define PROBE_PIN           (5U)

#define AUXOUTPUT0_PIN      (30u)
#define AUXOUTPUT1_PIN      (31u)

#if I2C_ENABLE
#define I2C_PORT    4
#define I2C_SCL4    (24u) // Not referenced, for info only
#define I2C_SDA4    (25u) // Not referenced, for info only
#endif

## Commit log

2023-06-25 mostly update documentation for laser board r5
2023-06-25 Rev5 design files; still need to generate a proper BOM and assembly docs
    [InputConditioning.kicad_sch, LaserBoard.kicad_pcb, LaserBoard.kicad_sch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]
2023-06-25 And that's why we write documentation - two small errors on the pcb
    [LaserBoard.kicad_pcb, LaserBoard.kicad_sch, LaserIO.kicad_sch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]
2023-07-01 BOM, readme update
    [LaserBoard.kicad_pcb, LaserBoard.kicad_sch, LaserBoardRev5-BOM.csv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]
2023-10-08 Rev 5a
    [LaserBoard.kicad_pcb, LaserBoard.kicad_sch, LaserBoardRev5a-BOM.csv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]
2023-10-27 Add new images, purge an old schematic sheet, and update the package of a component to match the datasheet.
    [InputConditioning.kicad_sch, LaserBoard.kicad_pcb, LaserIO.kicad_sch]

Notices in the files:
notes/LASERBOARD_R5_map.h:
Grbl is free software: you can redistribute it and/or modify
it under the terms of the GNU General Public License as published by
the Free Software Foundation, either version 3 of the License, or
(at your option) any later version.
